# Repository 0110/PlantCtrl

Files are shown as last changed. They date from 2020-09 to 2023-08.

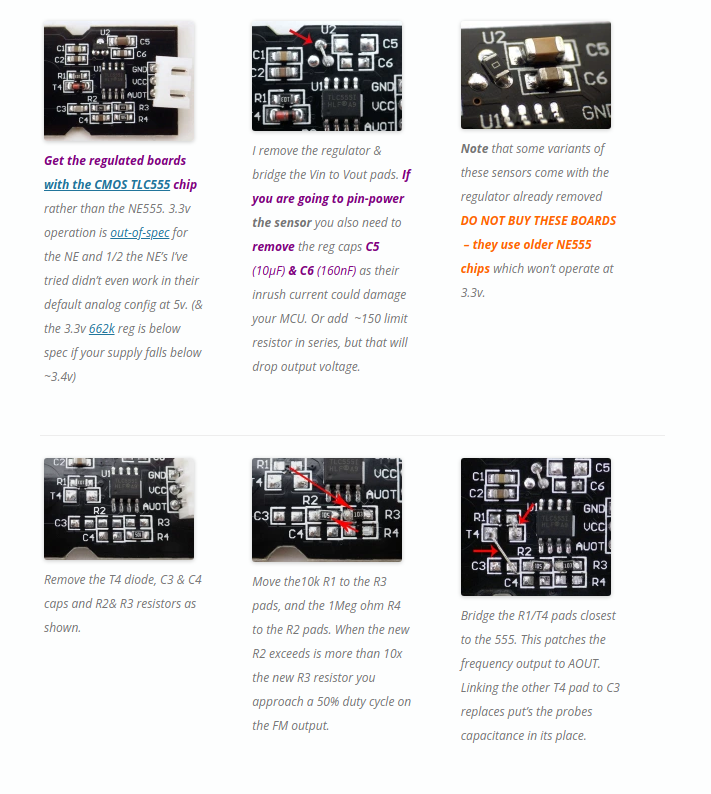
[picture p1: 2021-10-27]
hardware/sensor_mod.png

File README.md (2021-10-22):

# PlantCtrl

The following problems shall be solved with this project:
* Solar Powered
* Low Powered
* Plant monitoring
* Plant watering
* IoT

# Hardware
Open hardware design (powered by KiCAD).
The complete PCB is stored in the ***board*** sub directory.

There the following components are connected:
* ESP32 **16MB flash required**
* Lipo monitoring (DS2438)
* 7 moist sensors
* 7 pump
* DC-DC convert (generating voltage from Lipo for pumps)
* DS18B20 temperature sensors
* water level via laser distance sensor (VL53L0X)
* DS2438 battery monitor
* general purpose expansion pins

# Software
The firmware for the controller is stored in ***esp32*** sub directory.

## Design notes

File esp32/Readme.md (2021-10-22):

# PlantControl
## Hardware

Main processor
* ESP32 with 16MB Flash 

One-Wire
* Temperatur Sensor (DS18B20)
* Lipo-Monitoring (DS2438)

Lipo Protection
* Open drain 3.3V detector (CN61CN33 @ jlcpcb parts)

### Used Pins:
* See '''include/ControllerConfiguration.h'''

## Software
* MQTT topics

# Hardware
## Features
* Support for up to
 * 7 Moister sensors
 * 7 Pumps
 * Sensors
  * Solar powered (voltage)
  * Lipo-Powered (DS2438 for monitoring)
  * Temperature
  * Laser distance sensor [VL53L0X]
 * Custom GPIO

## Documentation of Power-Modes
https://lastminuteengineers.com/esp32-sleep-modes-power-consumption/#esp32-deep-sleep

gpio 17 only out no hold
gpio 16 only out no hold

## Additional hardware
solar charger 2A?
https://www.aliexpress.com/item/4000238259949.html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,searchweb201602_,searchweb201603_

MT3608 boost für pumpe
https://www.aliexpress.com/item/32925951391.html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,searchweb201602_,searchweb201603_

DS18B20 one wire temp sensor

# Features
## Empires Wunschliste
 * Pflanze
  * Pumpe
   * [x] Zeitspann (wann laufen darf)
   * [x] Helligkeitstrigger (Um den Morgen zum pumpen zu erkennen)
   * [-] Maximal Dauer zum Pumpen (als Zeit oder Milliliter)
   * [x] Zeitspanne zwischen zwei Pumpvorgängen
  * Moister sensor
   * [x] Schwellwert für Pumpe
* Tank
 * Füllstand Anzeige (in Liter)
 * Minimum Wasserstand (in cm damit Pumpen nicht leer laufen; enspricht 0 nutzbaren Liter)
 * [x] Maximaler Wasserstand des Tanks (in cm & Liter)

## Masterplan 2.0
 * Partitionslayout

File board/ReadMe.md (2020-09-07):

# ESP32 Plant Control Board

The board was built with manily through hole components for easy build and production with a mill.

## GPIO Mapping
See in the parent folder at **include/ControllerConfiguration.h**

## Routing
In order to use the the mill, the following parameter were used:
* Clearance 0.2mm
* Track width of 1.2mm or 1.0mm at minimum (when pins of a part are too close)

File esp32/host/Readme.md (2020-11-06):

# Configuration 
## File
Generate a file as, described in 
https://homieiot.github.io/homie-esp8266/docs/3.0.0/configuration/json-configuration-file/
For further details have a look at the Readme.md one level above.

## Upload
* Start ESP
* Login to Wifi, opened by the ESP
* Use the script to upload the configuration file
* restart the ESP

# Remote Upload

This script will allow you to send an OTA update to your device.

## Installation

Requirements are:
* paho-mqtt

## Usage

See ***upload-via-mqtt.sh***

# Remote Upload - Backend

## Usage

```text
usage: ota_updater.py [-h] -l BROKER_HOST -p BROKER_PORT [-u BROKER_USERNAME]
                      [-d BROKER_PASSWORD] [-t BASE_TOPIC] -i DEVICE_ID
                      firmware

ota firmware update scirpt for ESP8226 implemenation of the Homie mqtt IoT
convention.

positional arguments:
  firmware              path to the firmware to be sent to the device

arguments:
  -h, --help            show this help message and exit
  -l BROKER_HOST, --broker-host BROKER_HOST
                        host name or ip address of the mqtt broker
  -p BROKER_PORT, --broker-port BROKER_PORT
                        port of the mqtt broker
  -u BROKER_USERNAME, --broker-username BROKER_USERNAME
                        username used to authenticate with the mqtt broker
  -d BROKER_PASSWORD, --broker-password BROKER_PASSWORD
                        password used to authenticate with the mqtt broker
  -t BASE_TOPIC, --base-topic BASE_TOPIC
                        base topic of the homie devices on the broker
  -i DEVICE_ID, --device-id DEVICE_ID
                        homie device id
```

* `BROKER_HOST` and `BROKER_PORT` defaults to 127.0.0.1 and 1883 respectively if not set.
* `BROKER_USERNAME` and `BROKER_PASSWORD` are optional.
* `BASE_TOPIC` has to end with a slash, defaults to `homie/` if not set.

### Example:

```bash
python ota_updater.py -l localhost -u admin -d secure -t "homie/" -i "device-id" /path/to/firmware.bin
```

The Parameter can be extracted from the serial console
```serial
{} Stored configuration
  • Hardware device ID: 12345abcd
  • Device ID: MyDeviceId
  • Name: MyDeviceName
  • Device Stats Interval: 60 sec
  • Wi-Fi:
    ◦ SSID: MyWifi
    ◦ Password not shown
  • MQTT:
    ◦ Host: 192.168.0.2
    ◦ Port: 1883
    ◦ Base topic: /test/
    ◦ Auth? no
```

will result in the following command (when executed in this folder):
```bash
python ota_updater.py -l 192.168.0.2 -t "/test/" -i "MyDeviceId" ../.pio/build/esp32doit-devkit-v1/firmware.bin
```

### Source
https://github.com/homieiot/homie-esp8266/blob/develop/scripts/ota_updater

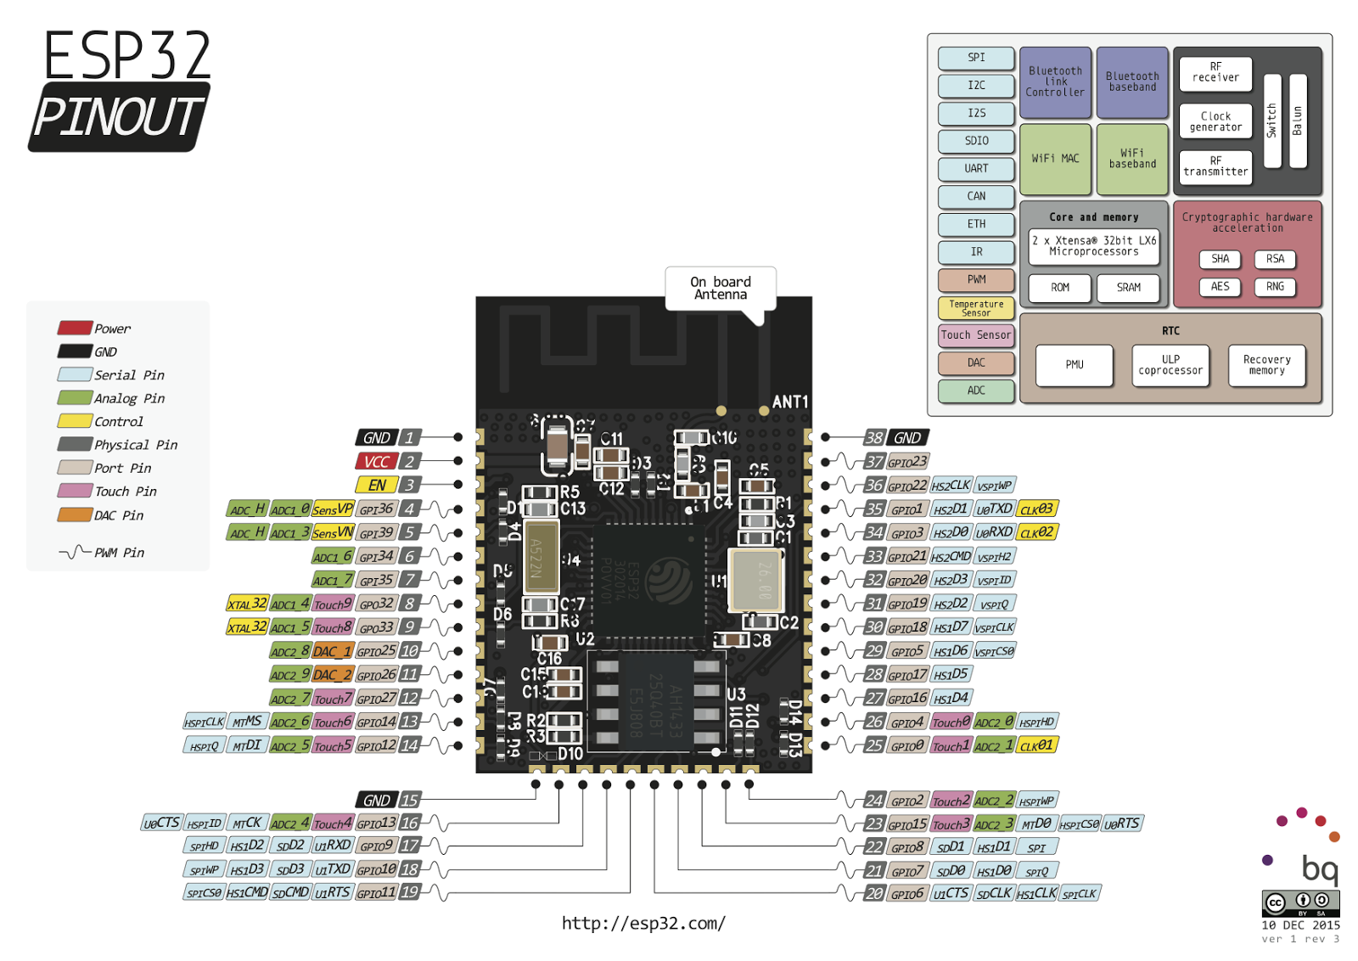
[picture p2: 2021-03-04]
sheets/esp32s.png

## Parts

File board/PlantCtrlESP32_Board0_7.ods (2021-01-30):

Reference | Value | Footprint | Datasheet | LCSC_PART_NUMBER | Field4 | Field5 | Field6 | DESCRIPTION | MANUFACTURER_PART_NUMBER
Shunt1 | 0.1 | Resistor_SMD:R_2512_6332Metric | ~ | C163067
R53 | 100 | Resistor_SMD:R_0805_2012Metric_Pad1.15x1.40mm_HandSolder | ~ | C17408
R11 | 270 | Resistor_SMD:R_0805_2012Metric_Pad1.15x1.40mm_HandSolder | ~ | C17590
R13 | 270 | Resistor_SMD:R_0805_2012Metric_Pad1.15x1.40mm_HandSolder | ~ | C17590
R15 | 270 | Resistor_SMD:R_0805_2012Metric_Pad1.15x1.40mm_HandSolder | ~ | C17590
R18 | 270 | Resistor_SMD:R_0805_2012Metric_Pad1.15x1.40mm_HandSolder | ~ | C17590
R30 | 270 | Resistor_SMD:R_0805_2012Metric_Pad1.15x1.40mm_HandSolder | ~ | C17590
R31 | 270 | Resistor_SMD:R_0805_2012Metric_Pad1.15x1.40mm_HandSolder | ~ | C17590
R5 | 270 | Resistor_SMD:R_0805_2012Metric_Pad1.15x1.40mm_HandSolder | ~ | C17590
R7 | 270 | Resistor_SMD:R_0805_2012Metric_Pad1.15x1.40mm_HandSolder | ~ | C17590
R9 | 270 | Resistor_SMD:R_0805_2012Metric_Pad1.15x1.40mm_HandSolder | ~ | C17590
R3 | 100k | Resistor_SMD:R_0805_2012Metric_Pad1.15x1.40mm_HandSolder | ~ | C702859
R54 | 100k | Resistor_SMD:R_0805_2012Metric_Pad1.15x1.40mm_HandSolder | ~ | C702859
C1 | 100n | Capacitor_SMD:C_0805_2012Metric_Pad1.15x1.40mm_HandSolder | ~ | C49678
C10 | 100n | Capacitor_SMD:C_0805_2012Metric_Pad1.15x1.40mm_HandSolder | ~ | C49678
C17 | 100n | Capacitor_SMD:C_0805_2012Metric_Pad1.15x1.40mm_HandSolder | ~ | C49678
C18 | 100n | Capacitor_SMD:C_0805_2012Metric_Pad1.15x1.40mm_HandSolder | ~ | C49678
C20 | 100n | Capacitor_SMD:C_0805_2012Metric_Pad1.15x1.40mm_HandSolder | ~ | C49678
C21 | 100n | Capacitor_SMD:C_0805_2012Metric_Pad1.15x1.40mm_HandSolder | ~ | C49678
C3 | 100n | Capacitor_SMD:C_0805_2012Metric_Pad1.15x1.40mm_HandSolder | ~ | C49678
C4 | 100n | Capacitor_SMD:C_0805_2012Metric_Pad1.15x1.40mm_HandSolder | ~ | C49678
C5 | 100n | Capacitor_SMD:C_0805_2012Metric_Pad1.15x1.40mm_HandSolder | ~ | C49678
C6 | 100n | Capacitor_SMD:C_0805_2012Metric_Pad1.15x1.40mm_HandSolder | ~ | C49678
C7 | 100n | Capacitor_SMD:C_0805_2012Metric_Pad1.15x1.40mm_HandSolder | ~ | C49678
C8 | 100n | Capacitor_SMD:C_0805_2012Metric_Pad1.15x1.40mm_HandSolder | ~ | C49678
C9 | 100n | Capacitor_SMD:C_0805_2012Metric_Pad1.15x1.40mm_HandSolder | ~ | C49678
R1 | 10k | Resistor_SMD:R_0805_2012Metric_Pad1.15x1.40mm_HandSolder | ~ | C212284
R12 | 10k | Resistor_SMD:R_0805_2012Metric_Pad1.15x1.40mm_HandSolder | ~ | C212284
R14 | 10k | Resistor_SMD:R_0805_2012Metric_Pad1.15x1.40mm_HandSolder | ~ | C212284
R16 | 10k | Resistor_SMD:R_0805_2012Metric_Pad1.15x1.40mm_HandSolder | ~ | C212284
R19 | 10k | Resistor_SMD:R_0805_2012Metric_Pad1.15x1.40mm_HandSolder | ~ | C212284
R2 | 10k | Resistor_SMD:R_0805_2012Metric_Pad1.15x1.40mm_HandSolder | ~ | C212284
R20 | 10k | Resistor_SMD:R_0805_2012Metric_Pad1.15x1.40mm_HandSolder | ~ | C212284
R22 | 10k | Resistor_SMD:R_0805_2012Metric_Pad1.15x1.40mm_HandSolder | ~ | C212284
R23 | 10k | Resistor_SMD:R_0805_2012Metric_Pad1.15x1.40mm_HandSolder | ~ | C212284
R24 | 10k | Resistor_SMD:R_0805_2012Metric_Pad1.15x1.40mm_HandSolder | ~ | C212284
R25 | 10k | Resistor_SMD:R_0805_2012Metric_Pad1.15x1.40mm_HandSolder | ~ | C212284
R27 | 10k | Resistor_SMD:R_0805_2012Metric_Pad1.15x1.40mm_HandSolder | ~ | C212284
R28 | 10k | Resistor_SMD:R_0805_2012Metric_Pad1.15x1.40mm_HandSolder | ~ | C212284
R32 | 10k | Resistor_SMD:R_0805_2012Metric_Pad1.15x1.40mm_HandSolder | ~ | C212284
R33 | 10k | Resistor_SMD:R_0805_2012Metric_Pad1.15x1.40mm_HandSolder | ~ | C212284
R35 | 1k | Resistor_SMD:R_0805_2012Metric_Pad1.15x1.40mm_HandSolder | ~ | C95781
R37 | 1k | Resistor_SMD:R_0805_2012Metric_Pad1.15x1.40mm_HandSolder | ~ | C95781
R4 | 10k | Resistor_SMD:R_0805_2012Metric_Pad1.15x1.40mm_HandSolder | ~ | C212284
R48 | 10k | Resistor_SMD:R_0805_2012Metric_Pad1.15x1.40mm_HandSolder | ~ | C212284
R58 | 10k | Resistor_SMD:R_0805_2012Metric_Pad1.15x1.40mm_HandSolder | ~ | C212284
R59 | 10k | Resistor_SMD:R_0805_2012Metric_Pad1.15x1.40mm_HandSolder | ~ | C212284
R6 | 10k | Resistor_SMD:R_0805_2012Metric_Pad1.15x1.40mm_HandSolder | ~ | C212284
R8 | 10k | Resistor_SMD:R_0805_2012Metric_Pad1.15x1.40mm_HandSolder | ~ | C212284
R21 | 19k-19.5K | Resistor_SMD:R_0805_2012Metric_Pad1.15x1.40mm_HandSolder | ~ | C17506
R29 | 1k | Resistor_SMD:R_0805_2012Metric_Pad1.15x1.40mm_HandSolder | ~ | C95781
R34 | 1k | Resistor_SMD:R_0805_2012Metric_Pad1.15x1.40mm_HandSolder | ~ | C95781
R36 | 1k | Resistor_SMD:R_0805_2012Metric_Pad1.15x1.40mm_HandSolder | ~ | C95781
R38 | 1k | Resistor_SMD:R_0805_2012Metric_Pad1.15x1.40mm_HandSolder | ~ | C95781
R39 | 1k | Resistor_SMD:R_0805_2012Metric_Pad1.15x1.40mm_HandSolder | ~ | C95781
R40 | 1k | Resistor_SMD:R_0805_2012Metric_Pad1.15x1.40mm_HandSolder | ~ | C95781
R41 | 1k | Resistor_SMD:R_0805_2012Metric_Pad1.15x1.40mm_HandSolder | ~ | C95781
R42 | 1k | Resistor_SMD:R_0805_2012Metric_Pad1.15x1.40mm_HandSolder | ~ | C95781
R43 | 1k | Resistor_SMD:R_0805_2012Metric_Pad1.15x1.40mm_HandSolder | ~ | C95781
R44 | 1k | Resistor_SMD:R_0805_2012Metric_Pad1.15x1.40mm_HandSolder | ~ | C95781
R45 | 1k | Resistor_SMD:R_0805_2012Metric_Pad1.15x1.40mm_HandSolder | ~ | C95781
R46 | 1k | Resistor_SMD:R_0805_2012Metric_Pad1.15x1.40mm_HandSolder | ~ | C95781
R47 | 1k | Resistor_SMD:R_0805_2012Metric_Pad1.15x1.40mm_HandSolder | ~ | C95781
R49 | 1k | Resistor_SMD:R_0805_2012Metric_Pad1.15x1.40mm_HandSolder | ~ | C95781
R50 | 1k | Resistor_SMD:R_0805_2012Metric_Pad1.15x1.40mm_HandSolder | ~ | C95781
R51 | 1k | Resistor_SMD:R_0805_2012Metric_Pad1.15x1.40mm_HandSolder | ~ | C95781
R52 | 1k | Resistor_SMD:R_0805_2012Metric_Pad1.15x1.40mm_HandSolder | ~ | C95781
C11 | 22uf | Capacitor_SMD:C_0805_2012Metric_Pad1.15x1.40mm_HandSolder | ~ | C45783
C12 | 22uf | Capacitor_SMD:C_0805_2012Metric_Pad1.15x1.40mm_HandSolder | ~ | C45783
C13 | 22uf | Capacitor_SMD:C_0805_2012Metric_Pad1.15x1.40mm_HandSolder | ~ | C45783
C14 | 22uf | Capacitor_SMD:C_0805_2012Metric_Pad1.15x1.40mm_HandSolder | ~ | C45783
C15 | 22uf | Capacitor_SMD:C_0805_2012Metric_Pad1.15x1.40mm_HandSolder | ~ | C45783
C16 | 22uf | Capacitor_SMD:C_0805_2012Metric_Pad1.15x1.40mm_HandSolder | ~ | C45783
C19 | 22uf | Capacitor_SMD:C_0805_2012Metric_Pad1.15x1.40mm_HandSolder | ~ | C45783
C2 | 22uf | Capacitor_SMD:C_0805_2012Metric_Pad1.15x1.40mm_HandSolder | ~ | C45783
D18 | 40V >2A | Diode_SMD:D_SOD-123F | ~ | C496544
D26 | 40V >2A | Diode_SMD:D_SOD-123F | ~ | C496544
D8 | 40V >2A | Diode_SMD:D_SOD-123F | ~ | C496544
R10 | 47k | Resistor_SMD:R_0805_2012Metric_Pad1.15x1.40mm_HandSolder | ~ | C17713
R17 | 47k | Resistor_SMD:R_0805_2012Metric_Pad1.15x1.40mm_HandSolder | ~ | C17713
L1 | 4A 5-22uH min DCR | Inductor_SMD:L_12x12mm_H4.5mm | ~ | C439398
R26 | 4k7 | Resistor_SMD:R_0805_2012Metric_Pad1.15x1.40mm_HandSolder | ~ | C17673
D10 | BAS40-04 | Package_TO_SOT_SMD:SOT-23 | http://www.vishay.com/docs/85701/bas40v.pdf | C397601
D11 | BAS40-04 | Package_TO_SOT_SMD:SOT-23 | http://www.vishay.com/docs/85701/bas40v.pdf | C397601
D12 | BAS40-04 | Package_TO_SOT_SMD:SOT-23 | http://www.vishay.com/docs/85701/bas40v.pdf | C397601
D13 | BAS40-04 | Package_TO_SOT_SMD:SOT-23 | http://www.vishay.com/docs/85701/bas40v.pdf | C397601
D14 | BAS40-04 | Package_TO_SOT_SMD:SOT-23 | http://www.vishay.com/docs/85701/bas40v.pdf | C397601
D15 | BAS40-04 | Package_TO_SOT_SMD:SOT-23 | http://www.vishay.com/docs/85701/bas40v.pdf | C397601
D16 | BAS40-04 | Package_TO_SOT_SMD:SOT-23 | http://www.vishay.com/docs/85701/bas40v.pdf | C397601
D17 | BAS40-04 | Package_TO_SOT_SMD:SOT-23 | http://www.vishay.com/docs/85701/bas40v.pdf | C397601
D19 | BAS40-04 | Package_TO_SOT_SMD:SOT-23 | http://www.vishay.com/docs/85701/bas40v.pdf | C397601
D20 | BAS40-04 | Package_TO_SOT_SMD:SOT-23 | http://www.vishay.com/docs/85701/bas40v.pdf | C397601
D21 | BAS40-04 | Package_TO_SOT_SMD:SOT-23 | http://www.vishay.com/docs/85701/bas40v.pdf | C397601
D22 | BAS40-04 | Package_TO_SOT_SMD:SOT-23 | http://www.vishay.com/docs/85701/bas40v.pdf | C397601
D23 | BAS40-04 | Package_TO_SOT_SMD:SOT-23 | http://www.vishay.com/docs/85701/bas40v.pdf | C397601
D24 | BAS40-04 | Package_TO_SOT_SMD:SOT-23 | http://www.vishay.com/docs/85701/bas40v.pdf | C397601
D25 | BAS40-04 | Package_TO_SOT_SMD:SOT-23 | http://www.vishay.com/docs/85701/bas40v.pdf | C397601
D9 | BAS40-04 | Package_TO_SOT_SMD:SOT-23 | http://www.vishay.com/docs/85701/bas40v.pdf | C397601
EXT_PWR1 | Conn_01x02 | Connector_JST:JST_XH_B2B-XH-A_1x02_P2.50mm_Vertical | ~
LIPO1 | Conn_01x02_Female | misc_footprints:BatteryHolder_Keystone_1042_1x18650 | ~
LIPO2 | Conn_01x02_Female | Connector_Wire:SolderWirePad_1x02_P5.08mm_Drill1.5mm | ~
PUMP0 | Conn_01x02_Female | Connector_JST:JST_EH_B2B-EH-A_1x02_P2.50mm_Vertical | ~
PUMP1 | Conn_01x02_Female | Connector_JST:JST_EH_B2B-EH-A_1x02_P2.50mm_Vertical | ~
PUMP2 | Conn_01x02_Female | Connector_JST:JST_EH_B2B-EH-A_1x02_P2.50mm_Vertical | ~
PUMP3 | Conn_01x02_Female | Connector_JST:JST_EH_B2B-EH-A_1x02_P2.50mm_Vertical | ~
PUMP4 | Conn_01x02_Female | Connector_JST:JST_EH_B2B-EH-A_1x02_P2.50mm_Vertical | ~
PUMP5 | Conn_01x02_Female | Connector_JST:JST_EH_B2B-EH-A_1x02_P2.50mm_Vertical | ~
PUMP6 | Conn_01x02_Female | Connector_JST:JST_EH_B2B-EH-A_1x02_P2.50mm_Vertical | ~
1WIRE1 | Conn_01x03 | Connector_JST:JST_EH_B3B-EH-A_1x03_P2.50mm_Vertical | ~
S0 | Conn_01x03_Male | Connector_JST:JST_EH_B3B-EH-A_1x03_P2.50mm_Vertical | ~
S1 | Conn_01x03_Male | Connector_JST:JST_EH_B3B-EH-A_1x03_P2.50mm_Vertical | ~
S2 | Conn_01x03_Male | Connector_JST:JST_EH_B3B-EH-A_1x03_P2.50mm_Vertical | ~
S3 | Conn_01x03_Male | Connector_JST:JST_EH_B3B-EH-A_1x03_P2.50mm_Vertical | ~
S4 | Conn_01x03_Male | Connector_JST:JST_EH_B3B-EH-A_1x03_P2.50mm_Vertical | ~
S5 | Conn_01x03_Male | Connector_JST:JST_EH_B3B-EH-A_1x03_P2.50mm_Vertical | ~
S6 | Conn_01x03_Male | Connector_JST:JST_EH_B3B-EH-A_1x03_P2.50mm_Vertical | ~
CUSTOM1 | Conn_01x04 | Connector_JST:JST_EH_B4B-EH-A_1x04_P2.50mm_Vertical | ~
DCDC1 | Conn_01x04 | Connector_PinSocket_2.54mm:PinSocket_1x04_P2.54mm_Vertical | ~
Hall1 | Conn_01x04 | ESP32:SR04M-2PinHeader_1x04_P2.54mm_Vertical | ~
SOLAR1 | Conn_01x04 | Connector_PinSocket_2.54mm:PinSocket_1x04_P2.54mm_Vertical | ~
I2C1 | Conn_01x04_Female | Connector_JST:JST_EH_B4B-EH-A_1x04_P2.50mm_Vertical | ~
GPIO1 | Conn_01x05_Female | Connector_JST:JST_EH_B5B-EH-A_1x05_P2.50mm_Vertical | ~
U1 | DS18B20 | Package_TO_SOT_THT:TO-92_Inline | http://datasheets.maximintegrated.com/en/ds/DS18B20.pdf
U2 | ds2438az+ | misc_footprints:ds2438az&plus_
IC1 | DW01 | misc_footprints:SOT95P280X135-6N |  | C14213 |  |  |  | ic | DW01
U5 | ESP32-WROOM-32D | RF_Module:ESP32-WROOM-32 | https://www.espressif.com/sites/default/files/documentation/esp32-wroom-32d_esp32-wroom-32u_datasheet_en.pdf | C529578
F1 | Fuse | Fuse:Fuseholder_Cylinder-5x20mm_Stelvio-Kontek_PTF78_Horizontal_Open | ~ | C58066
D2 | LED | LED_SMD:LED_0805_2012Metric_Pad1.15x1.40mm_HandSolder | ~ | C375452
D5 | LED | LED_SMD:LED_0805_2012Metric_Pad1.15x1.40mm_HandSolder | ~ | C375452
D6 | LED | LED_SMD:LED_0805_2012Metric_Pad1.15x1.40mm_HandSolder | ~ | C375452
D1 | LED_Blue | LED_SMD:LED_0805_2012Metric_Pad1.15x1.40mm_HandSolder | ~ | C205441
D3 | LED_Blue | LED_SMD:LED_0805_2012Metric_Pad1.15x1.40mm_HandSolder | ~ | C205441
D4 | LED_Blue | LED_SMD:LED_0805_2012Metric_Pad1.15x1.40mm_HandSolder | ~ | C205441
D7 | LED_Blue | LED_SMD:LED_0805_2012Metric_Pad1.15x1.40mm_HandSolder | ~ | C205441
Sensor1 | LED_green | LED_SMD:LED_0805_2012Metric_Pad1.15x1.40mm_HandSolder | ~ | C205442
Pumps1 | LED_red | LED_SMD:LED_0805_2012Metric_Pad1.15x1.40mm_HandSolder | ~ | C84256
U3 | LP38690DT-3.3 | ESP32:DPAK457P991X255-3N | IPC-7351B | C109045 | Texas Instruments | M | 2.55mm
Q1 | N-channel 30V 5A | Package_TO_SOT_SMD:SOT-23_Handsoldering |  | C350314 / C344010
Q10 | N-channel 30V 5A | Package_TO_SOT_SMD:SOT-23_Handsoldering |  | C350314 / C344010
Q11 | N-channel 30V 5A | Package_TO_SOT_SMD:SOT-23_Handsoldering |  | C350314 / C344010
Q12 | N-channel 30V 5A | Package_TO_SOT_SMD:SOT-23_Handsoldering |  | C350314 / C344010
Q2 | N-channel 30V 5A | Package_TO_SOT_SMD:SOT-23_Handsoldering |  | C350314 / C344010
Q3 | N-channel 30V 5A | Package_TO_SOT_SMD:SOT-23_Handsoldering |  | C350314 / C344010
Q4 | N-channel 30V 5A | Package_TO_SOT_SMD:SOT-23_Handsoldering |  | C350314 / C344010
Q5 | N-channel 30V 5A | Package_TO_SOT_SMD:SOT-23_Handsoldering |  | C350314 / C344010
Q6 | N-channel 30V 5A | Package_TO_SOT_SMD:SOT-23_Handsoldering |  | C350314 / C344010
Q7 | N-channel 30V 5A | Package_TO_SOT_SMD:SOT-23_Handsoldering |  | C350314 / C344010
Q8 | N-channel 30V 5A | Package_TO_SOT_SMD:SOT-23_Handsoldering |  | C350314 / C344010
Q9 | N-channel 30V 5A | Package_TO_SOT_SMD:SOT-23_Handsoldering |  | C350314
JP5 | NC | Jumper:SolderJumper-2_P1.3mm_Bridged_Pad1.0x1.5mm | ~
LED_SENS1 | NC | Jumper:SolderJumper-2_P1.3mm_Bridged_Pad1.0x1.5mm | ~
SOLAR_PWR1 | NC | Jumper:SolderJumper-2_P1.3mm_Bridged_Pad1.0x1.5mm | ~
Q_PWR1 | P-channel 50v 4A | Package_TO_SOT_SMD:SOT-23_Handsoldering |  | C344010
Q_PWR2 | P-channel 50v 4A | Package_TO_SOT_SMD:SOT-23_Handsoldering |  | C344010
Q_PWR3 | P-channel 50v 4A | Package_TO_SOT_SMD:SOT-23_Handsoldering |  | C344010
EXT_PWR2 | SolderJumper_2_Open | Jumper:SolderJumper-2_P1.3mm_Open_Pad1.0x1.5mm | ~
JP2 | SolderJumper_2_Open | Jumper:SolderJumper-2_P1.3mm_Open_Pad1.0x1.5mm | ~
OCP1 | SolderJumper_2_Open | Jumper:SolderJumper-2_P1.3mm_Open_Pad1.0x1.5mm | ~
SW1 | SW_Push | Button_Switch_SMD:SW_Push_1P1T_NO_CK_KMR2 | ~ | C72443
SW2 | SW_Push | Button_Switch_SMD:SW_Push_1P1T_NO_CK_KMR2 | ~ | C72443
U4 | SX1308 | misc_footprints:SOT-23-6 |  | C78162

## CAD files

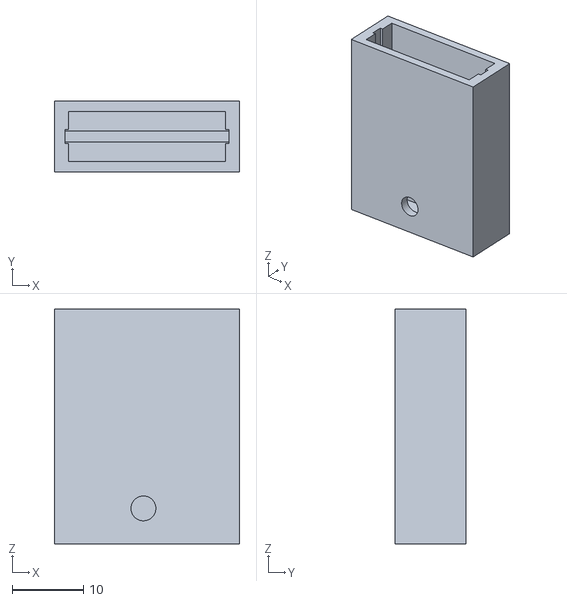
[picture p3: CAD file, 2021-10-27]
hardware/verguss form sensor v1.stl
26.0 x 10.0 x 33.0

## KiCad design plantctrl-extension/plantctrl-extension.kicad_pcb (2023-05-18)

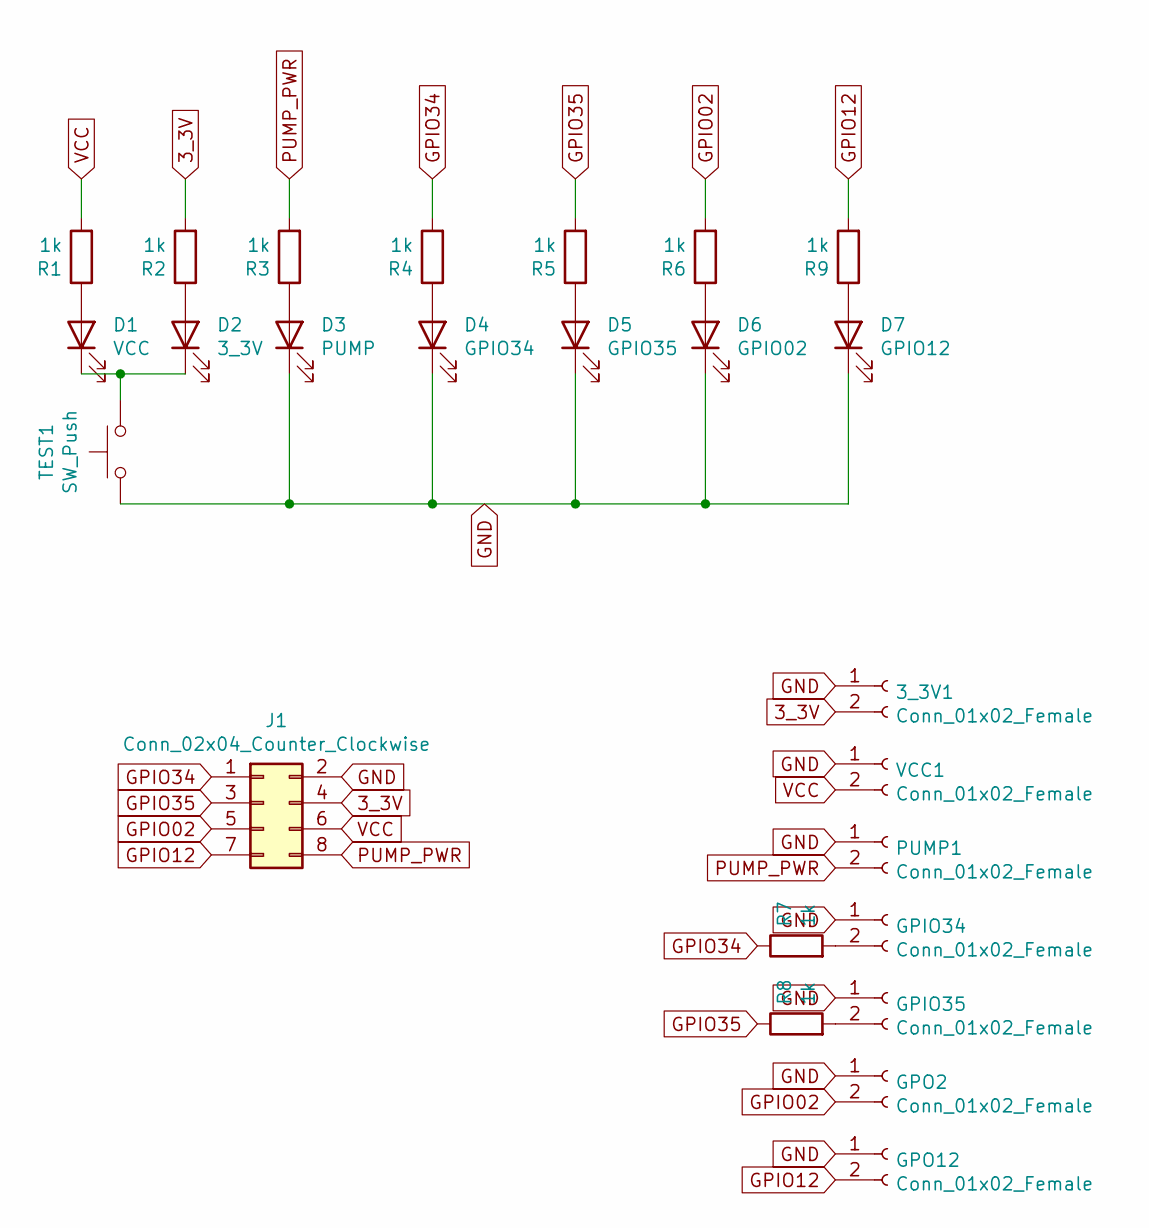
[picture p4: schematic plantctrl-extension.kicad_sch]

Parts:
3_3V1: Conn_01x02_Female; JST_EH_B2B-EH-A_1x02_P2.50mm_Vertical
D1: VCC; LED_0805_2012Metric; LCSC_PART_NUMBER C205441
D2: 3_3V; LED_0805_2012Metric; LCSC_PART_NUMBER C205441
D3: PUMP; LED_0805_2012Metric; LCSC_PART_NUMBER C205441
D4: GPIO34; LED_0805_2012Metric; LCSC_PART_NUMBER C205441
D5: GPIO35; LED_0805_2012Metric; LCSC_PART_NUMBER C205441
D6: GPIO02; LED_0805_2012Metric; LCSC_PART_NUMBER C205441
D7: GPIO12; LED_0805_2012Metric; LCSC_PART_NUMBER C205441
GPIO34, GPIO35: Conn_01x02_Female; JST_EH_B2B-EH-A_1x02_P2.50mm_Vertical
GPO2, GPO12: Conn_01x02_Female; JST_EH_B2B-EH-A_1x02_P2.50mm_Vertical
J1: Conn_02x04_Counter_Clockwise; PinSocket_2x04_P2.54mm_Vertical
PUMP1: Conn_01x02_Female; JST_EH_B2B-EH-A_1x02_P2.50mm_Vertical
R1, R2, R3, R4, R5, R6, R7, R8, R9: 1k; R_0805_2012Metric; LCSC_PART_NUMBER C95781
TEST1: SW_Push; SW_SPST_CK_RS282G05A3; LCSC_PART_NUMBER C72443
VCC1: Conn_01x02_Female; JST_EH_B2B-EH-A_1x02_P2.50mm_Vertical

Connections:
3_3V: 3_3V1.2, J1.4, R2.2
GND: 3_3V1.1, D3.1 (K), D4.1 (K), D5.1 (K), D6.1 (K), D7.1 (K), GPIO34.1, GPIO35.1, GPO2.1, GPO12.1, J1.2, PUMP1.1, TEST1.1, VCC1.1
GPIO02: GPO2.2, J1.5, R6.2
GPIO12: GPO12.2, J1.7, R9.2
GPIO34: J1.1, R4.2, R7.1
GPIO35: J1.3, R5.2, R8.1
unnamed: D1.2 (A), R1.1
unnamed: D2.2 (A), R2.1
unnamed: D3.2 (A), R3.1
unnamed: D4.2 (A), R4.1
unnamed: D5.2 (A), R5.1
unnamed: D6.2 (A), R6.1
unnamed: D7.2 (A), R9.1
unnamed: GPIO34.2, R7.2
unnamed: GPIO35.2, R8.2
unnamed: D1.1 (K), D2.1 (K), TEST1.2
PUMP_PWR: J1.8, PUMP1.2, R3.2
VCC: J1.6, R1.2, VCC1.2

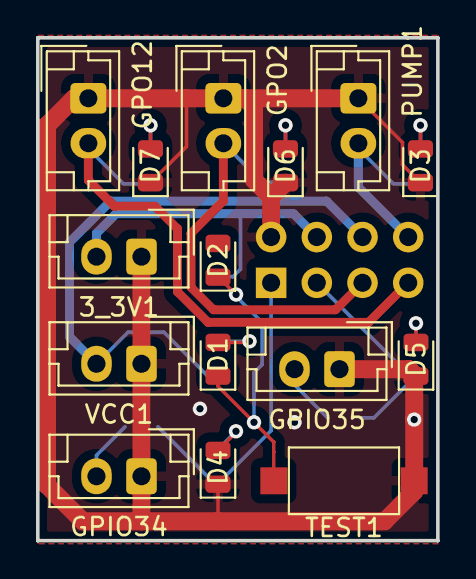
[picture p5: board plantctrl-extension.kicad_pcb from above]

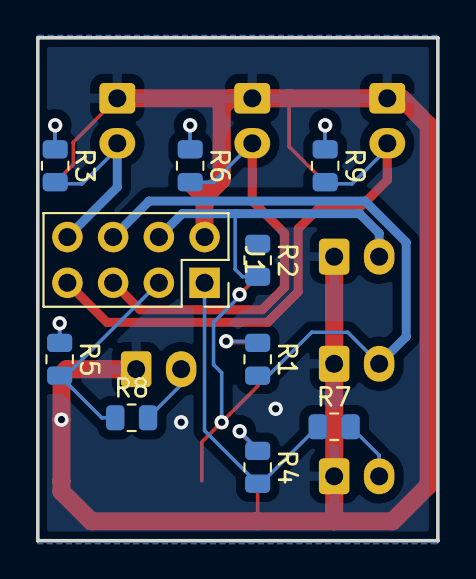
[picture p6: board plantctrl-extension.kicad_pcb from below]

Board: 2 copper layers, 22.2 x 27.9 mm, 25 parts (10 on the bottom side), 18 nets.

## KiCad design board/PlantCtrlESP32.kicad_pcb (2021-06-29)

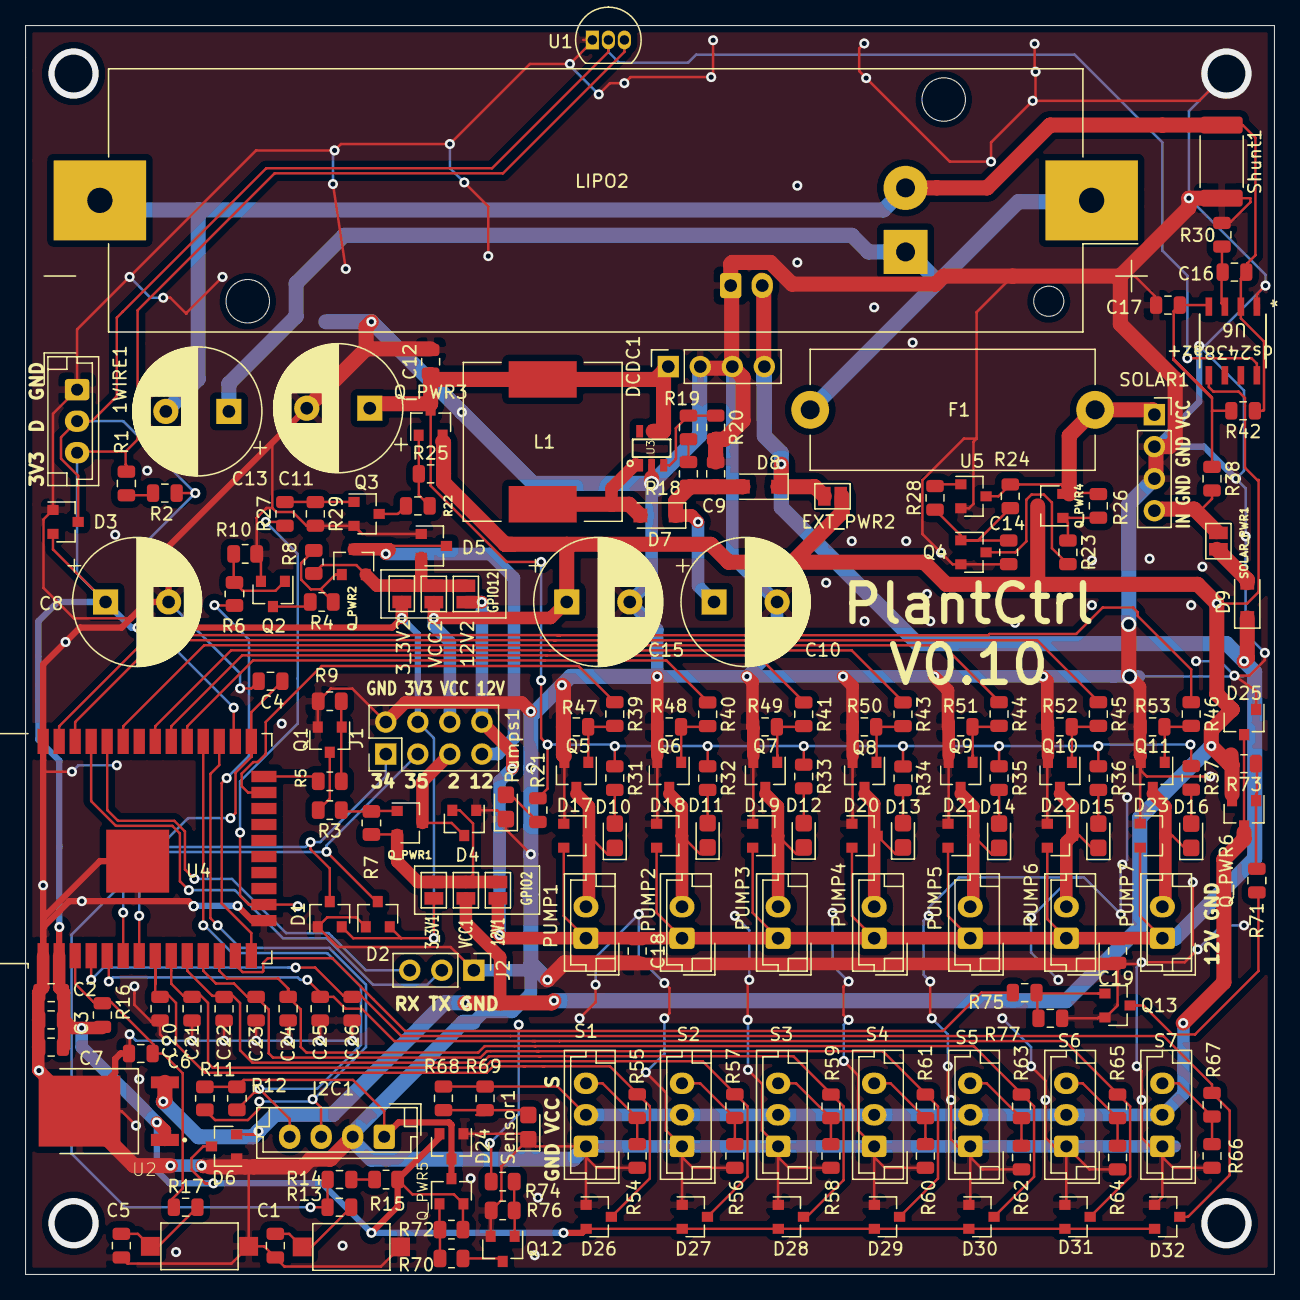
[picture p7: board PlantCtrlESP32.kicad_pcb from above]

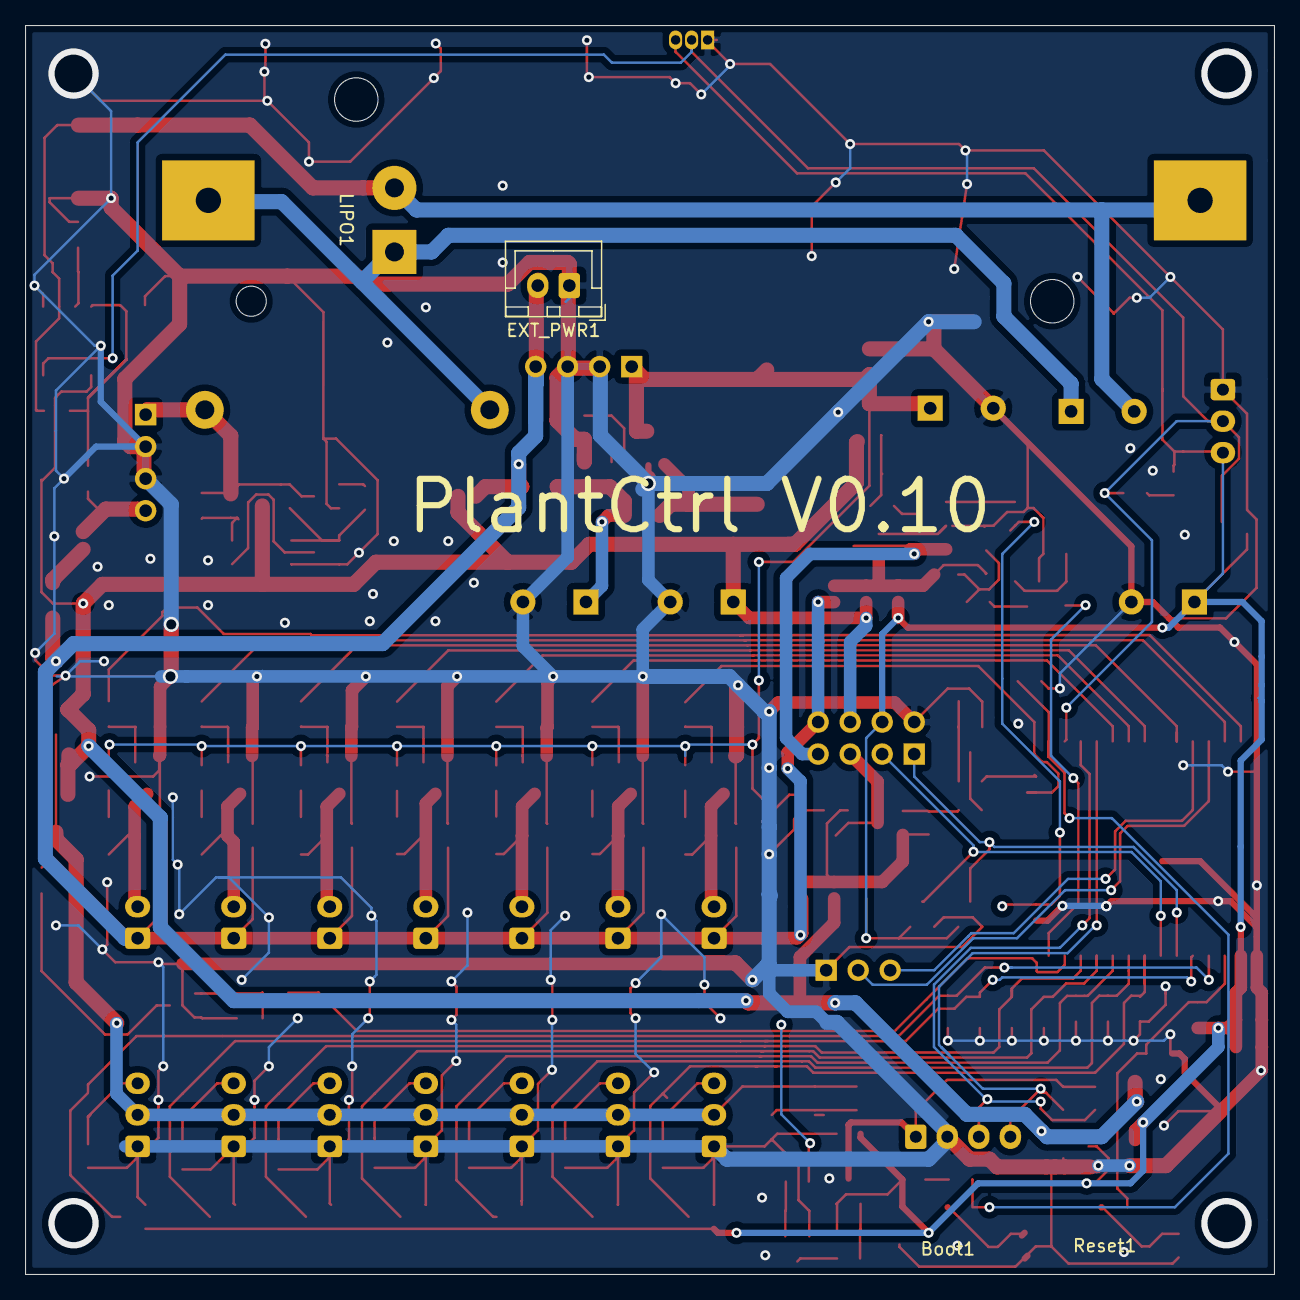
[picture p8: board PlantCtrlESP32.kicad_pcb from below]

Board: 2 copper layers, 99.1 x 99.1 mm, 198 parts (2 on the bottom side), 102 nets.

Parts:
1WIRE1: Conn_01x03; JST_EH_B3B-EH-A_1x03_P2.50mm_Vertical
3_3V1, 3_3V2, 12V1, 12V2: SolderJumper_2_Open; SolderJumper-2_P1.3mm_Open_Pad1.0x1.5mm
Boot1: Boot; SW_SPST_CK_RS282G05A3
C1, C2, C5, C14, C16, C17, C20, C21, C22, C23, C24, C25, C26: 100n; C_0805_2012Metric
C3, C4, C6, C7, C9, C12, C18, C19: 22uf; C_0805_2012Metric
C8, C10, C11, C13, C15: 1000uF; CP_Radial_D10.0mm_P5.00mm
D1, D2, D3, D4, D5, D6, D17, D18, D19, D20, D21, D22, D23, D24, D25, D26, D27, D28, D29, D30, D31, D32: BAS40-04; SOT-23
D7, D8, D9: 40V >2A; D_SOD-123F
D10, D12, D14, D16: LED_Blue; LED_0805_2012Metric_Castellated
D11, D13, D15: LED; LED_0805_2012Metric_Castellated
DCDC1: Conn_01x04; PinSocket_1x04_P2.54mm_Vertical
EXT_PWR1: Conn_01x02; JST_XH_B2B-XH-A_1x02_P2.50mm_Vertical
EXT_PWR2: SolderJumper_2_Open; SolderJumper-2_P1.3mm_Open_Pad1.0x1.5mm
F1: Fuse; Fuseholder_Cylinder-5x20mm_Stelvio-Kontek_PTF78_Horizontal_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
I2C1: Conn_01x04; JST_EH_B4B-EH-A_1x04_P2.50mm_Vertical
J1: Conn_02x04_Counter_Clockwise; PinHeader_2x04_P2.54mm_Vertical
J2: Conn_01x03_Female; PinHeader_1x03_P2.54mm_Vertical
L1: 4A 5-22uH min DCR; L_12x12mm_H4.5mm
LIPO1: Conn_01x02_Female; SolderWirePad_1x02_P5.08mm_Drill1.5mm
LIPO2: Conn_01x02_Female; BatteryHolder_Keystone_1042_1x18650
PUMP1, PUMP2, PUMP3, PUMP4, PUMP5, PUMP6, PUMP7: Conn_01x02_Female; JST_EH_B2B-EH-A_1x02_P2.50mm_Vertical
Pumps1: LED_red; LED_0805_2012Metric_Castellated
Q1, Q2, Q3, Q4, Q5, Q6, Q7, Q8, Q9, Q10, Q11, Q12, Q13: N-channel 30V 5A; SOT-23
Q_PWR1, Q_PWR2, Q_PWR3, Q_PWR4, Q_PWR5, Q_PWR6: P-channel 50v 4A; SOT-23
R1, R2, R3, R4, R5, R6, R13, R14, R15, R17, R20, R22, R23, R27, R28, R39, R40, R41, R42, R43, R44, R45, R46, R55, R57, R59, R61, R63, R65, R67, R70, R71, R74, R75: 1k; R_0805_2012Metric
R7, R8, R9, R10, R16, R18, R19, R25, R26, R29, R38, R47, R48, R49, R52, R53, R68, R69, R72, R73, R76, R77: 10k; R_0805_2012Metric
R11, R12: R; R_0805_2012Metric
R21, R31, R32, R33, R34, R35, R36, R37: 270; R_0805_2012Metric
R24, R30, R54, R56, R58, R60, R62, R64, R66: 100k; R_0805_2012Metric
R50, R51: 10K; R_0805_2012Metric
Reset1: SW_Push; SW_SPST_CK_RS282G05A3
S1, S2, S3, S4, S5, S6, S7: Conn_01x03_Male; JST_EH_B3B-EH-A_1x03_P2.50mm_Vertical
SOLAR1: Conn_01x04; PinSocket_1x04_P2.54mm_Vertical
SOLAR_PWR1: NO; SolderJumper-2_P1.3mm_Open_Pad1.0x1.5mm
Sensor1: LED_green; LED_0805_2012Metric_Castellated
Shunt1: 0.025; R_2512_6332Metric
U1: DS18B20; TO-92_Inline
U2: LP38690DT-3.3; DPAK457P991X255-3N
U3: SX1308; SOT-23-6
U4: ESP32-WROOM-32D; ESP32-WROOM-32
U5: CN61CN33; SOT-23
U6: ds2438az+; ds2438az&plus_
VCC1, VCC2: SolderJumper_2_Open; SolderJumper-2_P1.3mm_Open_Pad1.0x1.5mm

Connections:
3_3V: 1WIRE1.3, 3_3V1.2, 3_3V2.2, C2.2, C3.1, C7.1, C8.1, D1.2, D2.2, D3.2, D6.3, D24.2, D26.2, D27.2, D28.2, D29.2, D30.2, D31.2, D32.2, J1.4, Q_PWR5.2, R1.2, R15.2, R16.2, R72.2, U1.3, U2.1, U4.2
CUSTOM_GPIO2: R5.2, U4.24
CUSTOM_GPIO12: R6.2, U4.14
CUSTOM_GPIO34: D1.3, J1.1, U4.6
CUSTOM_GPIO35: D2.3, J1.3, U4.7
ESP_RX: J2.3, U4.34
ESP_TX: J2.2, U4.35
GND: 1WIRE1.1, Boot1.1, C1.1, C2.1, C3.2, C4.1, C5.1, C6.1, C7.2, C8.2, C9.2, C10.2, C11.2, C12.2, C14.1, C15.2, C17.2, C18.2, C19.2, C20.1, C21.1, C22.1, C23.1, C24.1, C25.1, C26.1, D1.1, D2.1, D3.1, D4.1, D5.1, D6.1, D17.1, D18.1, D19.1, D20.1, D21.1, D22.1, D23.1, D24.1, D25.1, D26.1, D27.1, D28.1, D29.1, D30.1, D31.1, D32.1, DCDC1.2, DCDC1.3, EXT_PWR1.1, I2C1.2, J1.2, J2.1, Pumps1.1, Q1.2, Q2.2, Q3.2, Q4.2, Q5.2, Q6.2, Q7.2, Q8.2, Q9.2, Q10.2, Q11.2, Q12.2, Q13.2, R9.2, R10.2, R20.2, R29.2, R30.1, R47.2, R48.1, R49.2, R50.2, R51.2, R52.2, R53.2, R54.1, R56.1, R58.1, R60.1, R62.1, R64.1, R66.1, R76.2, R77.2, Reset1.1, S1.1, S2.1, S3.1, S4.1, S5.1, S6.1, S7.1, SOLAR1.2, SOLAR1.3, Sensor1.1, Shunt1.2, U1.1, U2.4, U3.2, U4.1, U4.15, U4.38, U4.39, U5.2, U6.1
unnamed: 3_3V1.1, 12V1.1, D4.2, Q_PWR1.2, R7.2, VCC1.1
unnamed: 3_3V2.1, 12V2.1, D5.2, Q_PWR2.2, R8.2, VCC2.1
unnamed: Boot1.2, C1.2, R13.2
unnamed: C4.2, R13.1, R14.1, U4.25
unnamed: C5.2, R17.2, Reset1.2
unnamed: C6.2, R16.1, R17.1, U4.3
unnamed: C9.1, C10.1, D7.1, D8.2, R18.1
unnamed: C14.2, Q4.1, R24.2, R28.1
unnamed: C16.1, R30.2, U6.3
unnamed: C17.1, R38.1, R42.2, U6.4
unnamed: D4.3, J1.5, Q_PWR1.3
unnamed: D5.3, J1.7, Q_PWR2.3
unnamed: D7.2, L1.2, U3.1
unnamed: D9.2, SOLAR_PWR1.1
unnamed: D10.2, R31.2
unnamed: D11.2, R32.2
unnamed: D12.2, R33.2
unnamed: D13.2, R34.2
unnamed: D14.2, R35.2
unnamed: D15.2, R36.2
unnamed: D16.2, R37.2
unnamed: Pumps1.2, R21.2
unnamed: Q1.1, R5.1, R9.1
unnamed: Q1.3, R3.2
unnamed: Q2.1, R6.1, R10.1
unnamed: Q2.3, R4.2
unnamed: Q3.1, R27.1, R29.1
unnamed: Q3.3, R22.2
unnamed: Q4.3, R23.2
unnamed: Q5.1, R39.2, R47.1
unnamed: Q6.1, R40.2, R48.2
unnamed: Q7.1, R41.2, R49.1
unnamed: Q8.1, R43.2, R50.1
unnamed: Q9.1, R44.2, R51.1
unnamed: Q10.1, R45.2, R52.1
unnamed: Q11.1, R46.2, R53.1
unnamed: Q12.1, R74.1, R76.1
unnamed: Q12.3, R70.2
unnamed: Q13.1, R75.1, R77.1
unnamed: Q13.3, R71.2
unnamed: Q_PWR1.1, R3.1, R7.1
unnamed: Q_PWR2.1, R4.1, R8.1
unnamed: Q_PWR3.1, R22.1, R25.1
unnamed: Q_PWR4.1, R23.1, R26.1
unnamed: Q_PWR5.1, R70.1, R72.1
unnamed: Q_PWR6.1, R71.1, R73.1
unnamed: R1.1, R2.1
unnamed: R14.2, R15.1
unnamed: R18.2, R19.1
unnamed: R19.2, R20.1, U3.3
unnamed: R28.2, U5.1
unnamed: R54.2, R55.1, S1.3
unnamed: R56.2, R57.1, S2.3
unnamed: R58.2, R59.1, S3.3
unnamed: R60.2, R61.1, S4.3
unnamed: R62.2, R63.1, S5.3
unnamed: R64.2, R65.1, S6.3
unnamed: R66.2, R67.1, S7.3
unnamed: R68.1, R69.1, Sensor1.2
PLANT0_MOIST: C20.2, D26.3, R55.2, U4.8
PLANT0_PUMP: D10.1, D17.3, PUMP1.2, Q5.3
PLANT1_MOIST: C21.2, D27.3, R57.2, U4.9
PLANT1_PUMP: D11.1, D18.3, PUMP2.2, Q6.3
PLANT2_MOIST: C22.2, D28.3, R59.2, U4.10
PLANT2_PUMP: D12.1, D19.3, PUMP3.2, Q7.3
PLANT3_MOIST: C23.2, D29.3, R61.2, U4.11
PLANT3_PUMP: D13.1, D20.3, PUMP4.2, Q8.3
PLANT4_MOIST: C24.2, D30.3, R63.2, U4.12
PLANT4_PUMP: D14.1, D21.3, PUMP5.2, Q9.3
PLANT5_MOIST: C25.2, D31.3, R65.2, U4.5
PLANT5_PUMP: D15.1, D22.3, PUMP6.2, Q10.3
PLANT6_MOIST: C26.2, D32.3, R67.2, U4.4
PLANT6_PUMP: D16.1, D23.3, PUMP7.2, Q11.3
PLANT_CTRL_PUMP_0: R39.1, U4.23
PLANT_CTRL_PUMP_1: R40.1, U4.29
PLANT_CTRL_PUMP_2: R41.1, U4.30
PLANT_CTRL_PUMP_3: R43.1, U4.31
PLANT_CTRL_PUMP_4: R44.1, U4.33
PLANT_CTRL_PUMP_5: R45.1, U4.36
PLANT_CTRL_PUMP_6: R46.1, U4.37
PUMP_ENABLE: R27.2, U4.16
PUMP_PWR: 12V1.2, 12V2.2, C18.1, C19.1, D8.1, D9.1, D17.2, D18.2, D19.2, D20.2, D21.2, D22.2, D23.2, DCDC1.4, EXT_PWR1.2, EXT_PWR2.1, J1.8, PUMP1.1, PUMP2.1, PUMP3.1, PUMP4.1, PUMP5.1, PUMP6.1, PUMP7.1
PWR_I2C: D24.3, I2C1.1, Q_PWR5.3, R11.1, R12.1
PWR_PUMP_CONVERTER: C11.1, C12.1, DCDC1.1, L1.1, Q_PWR3.3, R21.1, R31.1, R32.1, R33.1, R34.1, R35.1, R36.1, R37.1, U3.4, U3.5
PWR_SENSORS: D25.3, Q_PWR6.3, R68.2, R69.2, S1.2, S2.2, S3.2, S4.2, S5.2, S6.2, S7.2
Rsense+: C13.2, C16.2, LIPO1.2, LIPO2.2, R42.1, Shunt1.1, U6.2
SCL: I2C1.3, R11.2, U4.27
SDA: I2C1.4, R12.2, U4.28
SENSORS_ENABLE: R74.2, R75.2, U4.13
SOLAR_IN: R38.2, SOLAR1.4, SOLAR_PWR1.2
Temp: 1WIRE1.2, D3.3, R2.2, U1.2, U4.26, U6.8
VCC: C15.1, D6.2, D25.2, EXT_PWR2.2, J1.6, Q_PWR3.2, Q_PWR4.3, Q_PWR6.2, R25.2, R73.2, U2.3, U6.5, VCC1.2, VCC2.2
VCC_BATT: C13.1, F1.2, LIPO1.1, LIPO2.1
VCC_FUSED_ALWAYS: F1.1, Q_PWR4.2, R24.1, R26.2, SOLAR1.1, U5.3

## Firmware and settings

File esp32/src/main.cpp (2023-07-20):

/** \addtogroup Controller
 *  @{
 *
 * @file main.cpp
 * @author Ollo
 * @brief PlantControl
 * @version 0.1
 * @date 2020-05-01
 *
 * @copyright Copyright (c) 2020
 */

/******************************************************************************
 *                                     INCLUDES
 ******************************************************************************/
#define CONFIG_APP_ROLLBACK_ENABLE
#include "LogDefines.h"
#include "FileUtils.h"
#include "TimeUtils.h"
#include "PlantCtrl.h"
#include "ControllerConfiguration.h"
#include "HomieConfiguration.h"
#include "DallasTemperature.h"
#include <Homie.h>
#include "time.h"
#include "esp_sleep.h"
#include "RunningMedian.h"
#include "WakeReason.h"
#include <stdint.h>
#include <math.h>
#include <OneWire.h>
#include "DS2438.h"
#include "soc/soc.h"
#include "soc/rtc_cntl_reg.h"
#include <Wire.h>
#include <VL53L0X.h>
#include "driver/pcnt.h"
#include "MQTTUtils.h"
#include "esp_ota_ops.h"
#include "Arduino.h"

extern "C" bool verifyRollbackLater(){
    return true;
}

#if defined(TIMED_LIGHT_PIN)
#include "ulp-pwm.h"
#endif

/******************************************************************************
 *                                     DEFINES
 ******************************************************************************/
#define AMOUNT_SENOR_QUERYS 8
#define MAX_TANK_DEPTH 5000
#define REBOOT_LOOP_DETECTION_ERROR 5

/******************************************************************************
 *                            FUNCTION PROTOTYPES
 ******************************************************************************/

int determineNextPump(bool lowLight);
void plantcontrol();
void readPowerSwitchedSensors();
bool determineTimedLightState(bool lowLight);
bool otaRunning = false;

/******************************************************************************
 *                       NON VOLATILE VARIABLES in DEEP SLEEP
 ******************************************************************************/
#if defined(TIMED_LIGHT_PIN)
RTC_DATA_ATTR bool timedLightLowVoltageTriggered = false; /**remember if it was shut down due to voltage level */
#endif                                                    // TIMED_LIGHT_PIN

RTC_DATA_ATTR long rtcLastWateringPlant[MAX_PLANTS] = {0};
RTC_DATA_ATTR long consecutiveWateringPlant[MAX_PLANTS] = {0};

/******************************************************************************
 *                            LOCAL VARIABLES
 ******************************************************************************/
bool volatile mDownloadMode = false; /**< Controller must not sleep */
bool volatile mSensorsRead = false;  /**< Sensors are read without Wifi or MQTT */
int volatile pumpToRun = -1;         /** pump to run  at the end of the cycle */
int volatile selfTestPumpRun = -1;   /** pump to run  at the end of the cycle */

bool mConfigured = false;
long nextBlink = 0; /**< Time needed in main loop to support expected blink code */

RunningMedian waterRawSensor = RunningMedian(WATERSENSOR_CYCLE);
float mSolarVoltage = 0.0f; /**< Voltage from solar panels */
float mBatteryVoltage = 0.0f; /**< Voltage from lipo */
unsigned long setupFinishedTimestamp;

bool pumpStarted = false;
long pumpTarget = -1;
long pumpStartTime = 0;
long lastSendPumpUpdate = 0;
#ifdef FLOWMETER_PIN
long pumpTargetMl = -1;
#endif

float waterTemp = 30;

/*************************** Hardware abstraction *****************************/

OneWire oneWire(SENSOR_ONEWIRE);
DallasTemperature sensors(&oneWire);
DS2438 battery(&oneWire, 0.0333333f, AMOUNT_SENOR_QUERYS);
VL53L0X tankSensor;

#ifndef PLANT0_SENSORTYPE
#error "Sensor type must be specified, see HomieTypes.h - Sensor types"
#endif
#ifndef PLANT1_SENSORTYPE
#error "Sensor type must be specified, see HomieTypes.h - Sensor types"
#endif
#ifndef PLANT2_SENSORTYPE
#error "Sensor type must be specified, see HomieTypes.h - Sensor types"
#endif
#ifndef PLANT3_SENSORTYPE
#error "Sensor type must be specified, see HomieTypes.h - Sensor types"
#endif
#ifndef PLANT4_SENSORTYPE
#error "Sensor type must be specified, see HomieTypes.h - Sensor types"
#endif
#ifndef PLANT5_SENSORTYPE
#error "Sensor type must be specified, see HomieTypes.h - Sensor types"
#endif
#ifndef PLANT6_SENSORTYPE
#error "Sensor type must be specified, see HomieTypes.h - Sensor types"
#endif

Plant mPlants[MAX_PLANTS] = {
    Plant(SENSOR_PLANT0, OUTPUT_PUMP0, 0, &plant0, &mSetting0, PLANT0_SENSORTYPE),
    Plant(SENSOR_PLANT1, OUTPUT_PUMP1, 1, &plant1, &mSetting1, PLANT1_SENSORTYPE),
    Plant(SENSOR_PLANT2, OUTPUT_PUMP2, 2, &plant2, &mSetting2, PLANT2_SENSORTYPE),
    Plant(SENSOR_PLANT3, OUTPUT_PUMP3, 3, &plant3, &mSetting3, PLANT3_SENSORTYPE),
    Plant(SENSOR_PLANT4, OUTPUT_PUMP4, 4, &plant4, &mSetting4, PLANT4_SENSORTYPE),
    Plant(SENSOR_PLANT5, OUTPUT_PUMP5, 5, &plant5, &mSetting5, PLANT5_SENSORTYPE),
    Plant(SENSOR_PLANT6, OUTPUT_PUMP6, 6, &plant6, &mSetting6, PLANT6_SENSORTYPE)};

/******************************************************************************
 *                            LOCAL FUNCTIONS
 ******************************************************************************/

void finsihedCycleSucessfully()
{
  const esp_partition_t *running = esp_ota_get_running_partition();
  esp_ota_img_states_t ota_state;
  if (esp_ota_get_state_partition(running, &ota_state) == ESP_OK)
  {
    log(LOG_LEVEL_INFO, "Get State Partition was Successfull", LOG_BOOT_ERROR_DETECTION); 
    
    if(ota_state == ESP_OTA_IMG_UNDEFINED){
      log(LOG_LEVEL_INFO, "ESP_OTA_IMG_UNDEFINED should not happen with rollback", LOG_BOOT_ERROR_DETECTION);
    }
    if(ota_state == ESP_OTA_IMG_NEW){
      log(LOG_LEVEL_INFO, "ESP_OTA_IMG_NEW", LOG_BOOT_ERROR_DETECTION);
    }
    if(ota_state == ESP_OTA_IMG_INVALID){
      log(LOG_LEVEL_INFO, "ESP_OTA_IMG_INVALID", LOG_BOOT_ERROR_DETECTION);
    }
    if(ota_state == ESP_OTA_IMG_VALID){
      log(LOG_LEVEL_INFO, "ESP_OTA_IMG_VALID", LOG_BOOT_ERROR_DETECTION);
    }
    if (ota_state == ESP_OTA_IMG_PENDING_VERIFY)
    {
      log(LOG_LEVEL_INFO, "ESP_OTA_IMG_PENDING_VERIFY Diagnostics completed successfully! Marking as valid", LOG_BOOT_ERROR_DETECTION);
      esp_ota_mark_app_valid_cancel_rollback();
    }
  }
}

void espDeepSleep(bool afterPump = false)
{
  if (mDownloadMode)
  {
    log(LOG_LEVEL_DEBUG, "abort deepsleep, DownloadMode active", LOG_DEBUG_CODE);
    // if we manage to get to the download mode, the device can be restored
    finsihedCycleSucessfully();
    return;
  }
  if (aliveWasRead())
  {
    for (int i = 0; i < 10; i++)
    {
      long cTime = getCurrentTime();
      if (cTime < 100000)
      {
        delay(100);
      }
      else
      {
        break;
      }
    }
    if (getCurrentTime() < 100000)
    {
      log(LOG_LEVEL_DEBUG, "NTP timeout before deepsleep", LOG_DEBUG_CODE);
    }
  }

  esp_sleep_pd_config(ESP_PD_DOMAIN_RTC_PERIPH, ESP_PD_OPTION_ON);

  long secondsToSleep = -1;

  if (afterPump)
  {
    log(LOG_LEVEL_INFO, "AfterPump Cycle Resume", LOG_SLEEP_CYCLE);
    secondsToSleep = 1;
  }
  else
  {
    if (mBatteryVoltage < VOLT_MIN_BATT) 
    {
      log(LOG_LEVEL_INFO, String(String(mBatteryVoltage) + "V! Almost empty -> deepSleepNight " + String(LOWVOLT_SLEEP_FACTOR)) + " times", LOG_SLEEP_LOWVOLTAGE);
      /* use the largest sleeping duration */
      if (deepSleepNightTime.get() > deepSleepTime.get()) {
        secondsToSleep = (deepSleepNightTime.get() * LOWVOLT_SLEEP_FACTOR);
      } else {
        secondsToSleep = (deepSleepTime.get() * LOWVOLT_SLEEP_FACTOR);
      }
      /* sleep at least several minutes, so the solar panel can charge the battery */
      if (secondsToSleep < LOWVOLT_SLEEP_MINIMUM) {
        secondsToSleep = LOWVOLT_SLEEP_MINIMUM;
      }
    }
    else if (mSolarVoltage < SOLAR_CHARGE_MIN_VOLTAGE)
    {
      log(LOG_LEVEL_INFO, String(String(mSolarVoltage) + "V! Low light -> deepSleepNight"), LOG_SLEEP_NIGHT);
      secondsToSleep = deepSleepNightTime.get();
    }
    else
    {
      log(LOG_LEVEL_INFO, "Sunny -> deepSleep", LOG_SLEEP_DAY);
      secondsToSleep = deepSleepTime.get();
    }
  }

  finsihedCycleSucessfully();
  /* sleep always at least one second */
  if (secondsToSleep < 0) {
    secondsToSleep = 1;
  }
  esp_sleep_enable_timer_wakeup((secondsToSleep * 1000U * 1000U));
  if (aliveWasRead())
  {
    delay(1000);
    Homie.prepareToSleep();
  }
  else
  {
    esp_deep_sleep_start();
  }
}

// requires homie being started
void readOneWireSensors()
{
  for (uint8_t i = 0; i < sensors.getDeviceCount(); i++)
  {
    uint8_t ds18b20Address[8];
    bool valid = false;
    float temp = -127;
    for (int retry = 0; retry < AMOUNT_SENOR_QUERYS && !valid; retry++)
    {
      bool validAddress = sensors.getAddress(ds18b20Address, i);
      if (validAddress && sensors.validFamily(ds18b20Address))
      {
        temp = sensors.getTempC(ds18b20Address);
        if (temp != -127)
        {
          valid = true;
        }
        else
        {
          delay(10);
        }
      }
    }

    if (!valid)
    {
      // wrong family or crc errors on each retry
      continue;
   }
   char buf[(sizeof(ds18b20Address) * 2) + 1]; /* additional byte for trailing terminator */
    snprintf(buf, sizeof(buf), "%.2X%.2X%.2X%.2X%.2X%.2X%.2X%.2X",
             ds18b20Address[0],
             ds18b20Address[1],
             ds18b20Address[2],
             ds18b20Address[3],
             ds18b20Address[4],
             ds18b20Address[5],
             ds18b20Address[6],
             ds18b20Address[7]);
   if (valid)
    {
      Serial << "DS18S20 Temperatur " << String(buf) << " : " << temp << " °C " << endl;
      if (strcmp(lipoSensorAddr.get(), buf) == 0)
      {
        mqttWrite(&sensorTemp, TEMPERATUR_SENSOR_LIPO, String(temp));
        Serial << "Lipo Temperatur " << temp << " °C " << endl;
      }
      if (strcmp(waterSensorAddr.get(), buf) == 0)
      {
        mqttWrite(&sensorTemp, TEMPERATUR_SENSOR_WATER, String(temp));
        Serial << "Water Temperatur " << temp << " °C " << endl;
        waterTemp = temp;
      }
      /* Always send the sensor address with the temperatur value */
      mqttWrite(&sensorTemp, String(buf), String(temp));
    }
    else
    {
      Serial << "DS18S20 sensor " << String(buf) << " could not be read " << temp << endl;
    }
  }

  battery.updateMultiple();
  mSolarVoltage = battery.getVoltage(BATTSENSOR_INDEX_SOLAR) * SOLAR_VOLT_FACTOR;

  Serial.flush();
}

/**
 * @brief Sensors, that are connected to GPIOs, mandatory for WIFI.
 * These sensors (ADC2) can only be read when no Wifi is used.
 */
void readPowerSwitchedSensors()
{
  for (int i = 0; i < MAX_PLANTS; i++)
  {
    Serial << "Sensor " << i << " mode:  " << mPlants[i].getSensorModeString() << endl;
  }
  digitalWrite(OUTPUT_ENABLE_SENSOR, HIGH);
  delay(50);
  for (int i = 0; i < MAX_PLANTS; i++)
  {
    mPlants[i].startMoistureMeasurement();
  }
  delay(MOISTURE_MEASUREMENT_DURATION);
  for (int i = 0; i < MAX_PLANTS; i++)
  {
    mPlants[i].stopMoistureMeasurement();
  }

  for (int i = 0; i < MAX_PLANTS; i++)
  {
    mPlants[i].blockingMoistureMeasurement();
  }

  for (int i = 0; i < MAX_PLANTS; i++)
  {
    Plant plant = mPlants[i];
    switch (plant.getSensorMode())
    {
      case FREQUENCY_MOD_RESISTANCE_PROBE: {
        Serial << "Plant " << i << " measurement: " << mPlants[i].getCurrentMoistureRaw() << " hz " << mPlants[i].getCurrentMoisturePCT() << "%" <<  endl;
        break;
      }
      case ANALOG_RESISTANCE_PROBE : {
        Serial << "Plant " << i << " measurement: " << mPlants[i].getCurrentMoistureRaw() << " mV " << mPlants[i].getCurrentMoisturePCT() << "%" <<  endl;
        break;
      }
      case NONE : {

      }
    }
  }

  Wire.begin(SENSOR_TANK_SDA, SENSOR_TANK_SCL);
  // Source: https://www.st.com/resource/en/datasheet/vl53l0x.pdf
  tankSensor.setAddress(0x52);
  tankSensor.setBus(&Wire);
  delay(50);
  Serial << "Distance sensor init" << endl;
  long start = millis();
  bool distanceReady = false;
  while ((start + WATERSENSOR_TIMEOUT) > millis())
  {
    if (tankSensor.init())
    {
      distanceReady = true;
      break;
    }
    else
    {
      delay(200);
    }
  }
  if (distanceReady)
  {
    waterRawSensor.clear();
    tankSensor.setSignalRateLimit(0.1);
    // increase laser pulse periods (defaults are 14 and 10 PCLKs)
    tankSensor.setVcselPulsePeriod(VL53L0X::VcselPeriodPreRange, 18);
    tankSensor.setVcselPulsePeriod(VL53L0X::VcselPeriodFinalRange, 14);
    tankSensor.setMeasurementTimingBudget(200000);
    Serial << "Distance sensor measuring" << endl;
    for (int readCnt = 0; readCnt < WATERSENSOR_CYCLE; readCnt++)
    
    {
      if (!tankSensor.timeoutOccurred())
      {
        uint16_t distance = tankSensor.readRangeSingleMillimeters();
        if (distance < MAX_TANK_DEPTH)
        {
          waterRawSensor.add(distance);
        }
      }
      delay(50);
    }
    Serial << "Distance sensor " << waterRawSensor.getMedian() << " mm" << endl;
  }
  else
  {
    log(LOG_LEVEL_WARN, LOG_TANKSENSOR_FAIL_DETECT, LOG_TANKSENSOR_FAIL_DETECT_CODE);
  }

  /* deactivate the sensors */
  digitalWrite(OUTPUT_ENABLE_SENSOR, LOW);
}

void onHomieEvent(const HomieEvent &event)
{
  switch (event.type)
  {
  case HomieEventType::READY_TO_SLEEP:
    esp_deep_sleep_start();
    break;
  case HomieEventType::SENDING_STATISTICS:
    break;
  case HomieEventType::MQTT_READY:
    if (mSensorsRead)
    {
      Serial.printf("Timeout occured... too late!\r\n");
      return;
    }
    mSensorsRead = true; // MQTT is working, deactivate timeout logic

    configTime(UTC_OFFSET_DE, UTF_OFFSET_DE_DST, ntpServer.get());
    startMQTTRoundtripTest();
    break;
  case HomieEventType::OTA_STARTED:
    for (int i = 0; i < MAX_PLANTS; i++)
    {
      mPlants[i].deactivatePump();
    }
    otaRunning = true;
    mDownloadMode = true;
    break;
  case HomieEventType::OTA_SUCCESSFUL:
    digitalWrite(OUTPUT_ENABLE_SENSOR, LOW);
    digitalWrite(OUTPUT_ENABLE_PUMP, LOW);
    ESP.restart();
    break;
  default:
    break;
  }
}
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
void loop()
{
  Homie.loop();
  /* Toggel Senor LED to visualize mode 3 */
  if (mDownloadMode)
  {
    if (nextBlink < millis())
    {
      digitalWrite(OUTPUT_ENABLE_SENSOR, !digitalRead(OUTPUT_ENABLE_SENSOR));
      if (mConfigured)
      {
        if (otaRunning)
        {
          nextBlink = millis() + 100;
        }
        else
        {
          nextBlink = millis() + 501;
        }
      }
      else
      {
        selfTest();
      }
    }
  }
  else
  {
    unsigned long timeSinceSetup = millis() - setupFinishedTimestamp;
    if ((timeSinceSetup > MQTT_TIMEOUT) && (!mSensorsRead))
    {
      mSensorsRead = true;
      /* Disable Wifi and put modem into sleep mode */
      WiFi.mode(WIFI_OFF);
      Serial << "Wifi mode set to " << WIFI_OFF << " mqqt was no reached within " << timeSinceSetup << "ms , fallback to offline mode " << endl;
      Serial.flush();
      plantcontrol();
    }
  }

  /** Timeout always stopping the ESP -> no endless power consumption */
  if (millis() > ESP_STALE_TIMEOUT && !mDownloadMode)
  {
    Serial << (millis() / 1000) << "not terminated watchdog reset" << endl;
    Serial.flush();
    esp_restart();
  }

  if (pumpToRun != -1)
  {
    pumpActiveLoop();
  }
}

/***
 * @fn plantcontrol
 * Main function, doing the logic
 */
void plantcontrol()
{
  if (aliveWasRead())
  {
    for (int i = 0; i < MAX_PLANTS; i++)
    {
      mPlants[i].postMQTTconnection();
      mPlants[i].setProperty("consecutivePumps").send(String(consecutiveWateringPlant[i]));
    }
  }

  readOneWireSensors();

  Serial << "W : " << waterRawSensor.getAverage() << " mm (" << String(waterLevelMax.get() - waterRawSensor.getAverage()) << " mm left)" << endl;

  mBatteryVoltage = battery.getVoltage(BATTSENSOR_INDEX_BATTERY);
  float chipTemp = battery.getTemperature();
  Serial << "Chip Temperatur " << chipTemp << " °C " << endl;

  if (aliveWasRead())
  {
    /* Publish water values, if available */
    if (waterRawSensor.getCount() > 0)
    {
      float remaining = (waterLevelMax.get() - waterRawSensor.getAverage());
      float actualDifference = waterLevelMax.get() - waterLevelMin.get();
      float ratio = remaining/actualDifference;
      sensorWater.setProperty("useable").send(String(actualDifference));
      if (!isnan(remaining))
      {
        /* measuring the distance from top -> smaller value means more water: */
        sensorWater.setProperty("remaining").send(String(ratio*100));
        
      }
      if (!isnan(waterRawSensor.getAverage()))
      {
        sensorWater.setProperty("distance").send(String(waterRawSensor.getAverage()));
      }
    }
    sensorLipo.setProperty("percent").send(String(100 * mBatteryVoltage / VOLT_MAX_BATT));
    sensorLipo.setProperty("volt").send(String(mBatteryVoltage));
    sensorLipo.setProperty("current").send(String(battery.getCurrent()));
    sensorLipo.setProperty("Ah").send(String(battery.getAh()));
    sensorLipo.setProperty("ICA").send(String(battery.getICA()));
    sensorLipo.setProperty("DCA").send(String(battery.getDCA()));
    sensorLipo.setProperty("CCA").send(String(battery.getCCA()));
    if (mSolarVoltage < SOLAR_MAX_VOLTAGE_POSSIBLE) {
      sensorSolar.setProperty("volt").send(String(mSolarVoltage));
    } else {
      log(LOG_LEVEL_INFO, String("Ignore unrealistc sun voltage" + String(mSolarVoltage) +"V"), LOG_SOLAR_CHARGER_MISSING);
    }
    sensorTemp.setProperty(TEMPERATUR_SENSOR_CHIP).send(String(chipTemp));
  }
  else
  {
    Serial.println("Skipping MQTT, offline mode");
    Serial.flush();
  }

bool isLowLight = (mSolarVoltage <= SOLAR_CHARGE_MAX_VOLTAGE);
#if defined(TIMED_LIGHT_PIN)
  
  bool shouldLight = determineTimedLightState(isLowLight);
  if(shouldLight){
    ulp_pwm_set_level(timedLightPowerLevel.get());
  }else {
    ulp_pwm_set_level(0);
  }

#endif // TIMED_LIGHT_PIN

  bool isLiquid = waterTemp > 5;
  bool hasWater = true; // By default activate the pump
  if (waterRawSensor.getCount() > 0)
  {
    //surface of water is still nearer the sensor than required to cover the pumps
    hasWater = waterRawSensor.getAverage() < waterLevelMin.get();
    if (waterRawSensor.getAverage() > waterLevelMax.get()) {
      log(LOG_LEVEL_ERROR, LOG_PUMP_FULLTANK_MESSAGE, LOG_PUMP_FULLTANK_CODE);
      hasWater = true;
    }
  }

  // FIXME no water warning message
  pumpToRun = determineNextPump(isLowLight);
  // early aborts
  if (pumpToRun != -1)
  {
    if(isLiquid){
      if (hasWater)
      {
        if (mDownloadMode)
        {
          log(LOG_LEVEL_INFO, LOG_PUMP_AND_DOWNLOADMODE, LOG_PUMP_AND_DOWNLOADMODE_CODE);
          pumpToRun = -1;
        } else {
          /* Pump can be used :) */
        }
      }
      else
      {
        log(LOG_LEVEL_ERROR, LOG_PUMP_BUTNOTANK_MESSAGE, LOG_PUMP_BUTNOTANK_CODE);
        pumpToRun = -1;
      }
    }
    else 
    {
        log(LOG_LEVEL_ERROR, LOG_VERY_COLD_WATER, LOG_VERY_COLD_WATER_CODE);
        pumpToRun = -1;
    }
  }

  // go directly to sleep, skipping the pump loop
  if (pumpToRun == -1)
  {
    espDeepSleep();
  }
}

/** @}*/

#ifdef TIMED_LIGHT_PIN
bool determineTimedLightState(bool lowLight)
{
  bool onlyAllowedWhenDark = timedLightOnlyWhenDark.get();
  long hoursStart = timedLightStart.get();
  long hoursEnd = timedLightEnd.get();

  // ntp missing
  if (getCurrentTime() < 10000)
  {
    timedLightNode.setProperty("state").send(String("Off, missing ntp"));
    return false;
  }
  if (onlyAllowedWhenDark && !lowLight)
  {
    timedLightNode.setProperty("state").send(String("Off, not dark"));
    timedLightLowVoltageTriggered = false;
    return false;
  }

  int curHour = getCurrentHour();

  bool condition1 = ((hoursStart > hoursEnd) &&
                     (curHour >= hoursStart || curHour <= hoursEnd));
  bool condition2 = /* Handle e.g. start = 8, end = 21 */

      ((hoursStart < hoursEnd) &&
       (curHour >= hoursStart && curHour <= hoursEnd));
  timedLightNode.setProperty("debug").send(String(curHour) + " " + String(hoursStart) + " " + String(hoursEnd) + " " + String(condition1) + " " + String(condition2));
  if (condition1 || condition2)
  {
    bool voltageOk = !timedLightLowVoltageTriggered && battery.getVoltage(BATTSENSOR_INDEX_BATTERY) >= timedLightVoltageCutoff.get();
    if (voltageOk || equalish(timedLightVoltageCutoff.get(), -1))
    {
      timedLightNode.setProperty("state").send(String("On"));
      return true;
    }
    else
    {
      timedLightNode.setProperty("state").send(String("Off, due to missing voltage"));
      timedLightLowVoltageTriggered = true;
      return false;
    }
  }
  else
  {
    timedLightNode.setProperty("state").send(String("Off, outside worktime"));
    return false;
  }
}

#endif

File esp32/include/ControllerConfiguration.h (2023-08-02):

/**
 * @file ControllerConfiguration.h
 * @author your name (you@domain.com)
 * @brief 
 * @version 0.1
 * @date 2020-05-30
 * 
 * @copyright Copyright (c) 2020
 * 
 * \mainpage Configuration of the controller
 * @{
 * Describe the used PINs of the controller
 *  
 * @subpage Controller
 * 
 * @subpage Homie
 * 
 * @subpage Configuration
 * 
 * There are several modes in the controller
 * \dot
 *  digraph Operationmode {
 *      ranksep=.75;
 *      poweroff [ label="off" ];
 *      mode1 [ label="Mode 1 - Sensor only", shape=box, width=2 ];
 *      mode2 [ label="Mode 2 - Wifi enabled", shape=box ];
 *      mode3 [ label="Mode 3 - Stay alive", shape=box ];
 *      mode1 -> mode2 [ label="wakeup reason", fontsize=10 ];
 *      mode1 -> mode2 [ label="Time duration", fontsize=10 ];
 *      mode2 -> mode3 [ label="Over the Air Update", fontsize=10 ];
 *      mode3 -> mode2 [ label="Over the Air Finished", fontsize=10 ];
 *      mode3 -> mode2 [ label="Mqtt Command", fontsize=10 ];
 *      mode2 -> mode3 [ label="Mqtt Command", fontsize=10 ];
 *      poweroff -> mode1 [ label="deep sleep wakeup", fontsize=10 ];
 *      mode1 -> poweroff [ label="enter deep sleep", fontsize=10 ];
 *      mode2 -> poweroff [ label="Mqtt queue empty", fontsize=10 ];
 *  }
 *  \enddot
 * 
 * Before entering Deep sleep the controller is configured with an wakeup time.
 * 
 * @}
 */
#ifndef CONTROLLER_CONFIG_H
#define CONTROLLER_CONFIG_H
/** \addtogroup GPIO Settings
 *  @{
 */
#define SENSOR_PLANT0 GPIO_NUM_32 /**< GPIO 32 (ADC1) */
#define SENSOR_PLANT1 GPIO_NUM_33 /**< GPIO 33 (ADC1) */
#define SENSOR_PLANT2 GPIO_NUM_25 /**< GPIO 25 (ADC2) */
#define SENSOR_PLANT3 GPIO_NUM_26 /**< GPIO 26 (ADC2) */
#define SENSOR_PLANT4 GPIO_NUM_27 /**< GPIO 27 (ADC2) */
#define SENSOR_PLANT5 GPIO_NUM_39 /**< SENSOR_VIN */
#define SENSOR_PLANT6 GPIO_NUM_36 /**< SENSOR_VP  */

#define OUTPUT_PUMP0 GPIO_NUM_15 /**< GPIO 15 */
#define OUTPUT_PUMP1 GPIO_NUM_5  /**< GPIO 5 */
#define OUTPUT_PUMP2 GPIO_NUM_18 /**< GPIO 18 */
#define OUTPUT_PUMP3 GPIO_NUM_19 /**< GPIO 19 */
#define OUTPUT_PUMP4 GPIO_NUM_21 /**< GPIO 21 */
#define OUTPUT_PUMP5 GPIO_NUM_22 /**< GPIO 22  */
#define OUTPUT_PUMP6 GPIO_NUM_23 /**< GPIO 23 */

#define OUTPUT_ENABLE_SENSOR GPIO_NUM_14 /**< GPIO 14 - Enable Sensors  */
#define OUTPUT_ENABLE_PUMP   GPIO_NUM_13 /**< GPIO 13 - Enable Pumps  */

#define SENSOR_ONEWIRE      GPIO_NUM_4 /**< GPIO 12 - Temperatur sensor, Battery and other cool onewire stuff */
#define SENSOR_TANK_SDA     GPIO_NUM_17 /**< GPIO 17 - water sensor SDA */ 
#define SENSOR_TANK_SCL     GPIO_NUM_16 /**< GPIO 16 - water sensor SCL */
#define BUTTON              GPIO_NUM_0  /**< GPIO 0 - Fix button of NodeMCU */

#define CUSTOM1_PIN1        GPIO_NUM_34   /** direct gpio */
#define CUSTOM1_PIN3        GPIO_NUM_35   /** direct gpio */
#define CUSTOM1_PIN5        GPIO_NUM_2   /** mosfet controlled */
#define CUSTOM1_PIN7        GPIO_NUM_12   /** mosfet controlled */

/* @} */

/** \addtogroup Configuration
 *  @{
 */

#ifdef FLOWMETER_PIN
    #define FLOWMETER_PULSES_PER_ML 2.2
    #define FIRMWARE_FEATURE1   "Flow"
#else
    #define FIRMWARE_FEATURE1   ""
#endif

#ifdef TIMED_LIGHT_PIN
    #define FIRMWARE_FEATURE2   "Light"
#else
    #define FIRMWARE_FEATURE2   ""
#endif

#define FIRMWARE_BASENAME "PlantControl"
#define FIRMWARE_NAME FIRMWARE_BASENAME FIRMWARE_FEATURE1 FIRMWARE_FEATURE2
#define FIRMWARE_VERSION "3.01 HW0.10b" 

#define MOIST_SENSOR_MAX_FRQ               5200 // 60kHz (500Hz margin)
#define MOIST_SENSOR_MIN_FRQ                500 // 0.5kHz (500Hz margin)

#define ANALOG_SENSOR_MAX_MV                1300 //successive approximation of good range
#define ANALOG_SENSOR_MIN_MV                100  //successive approximation of good range

#define SOLAR_VOLT_FACTOR           11
#define BATTSENSOR_INDEX_SOLAR      0
#define BATTSENSOR_INDEX_BATTERY    1

#define MQTT_TIMEOUT                (1000 * 60) /**< After 10 seconds, MQTT is expected to be connected */
#define ESP_STALE_TIMEOUT           (MQTT_TIMEOUT+(700*1000))

#define MAX_PLANTS          7
#define SOLAR_CHARGE_MIN_VOLTAGE    7   /**< Sun is rising (morning detected) */
#define SOLAR_CHARGE_MAX_VOLTAGE    9   /**< Sun is shining (noon)  */
#define SOLAR_MAX_VOLTAGE_POSSIBLE  100 /**< higher values are treated as not connected sensor  */
#define VOLT_MAX_BATT               4.2f
#define VOLT_MIN_BATT               3.0f    /**< Minimum battery voltage for normal operation */
#define LOWVOLT_SLEEP_FACTOR        3       /**< Factor for nightsleep delay, if the battery drops below minimum (@see VOLT_MIN_BATT) */
#define LOWVOLT_SLEEP_MINIMUM       1800    /**< At low voltage sleep at least for 30 minutes */

#define MAX_CONFIG_SETTING_ITEMS 100 /**< Parameter, that can be configured in Homie */
#define MAX_JSON_CONFIG_FILE_SIZE_CUSTOM 2500
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

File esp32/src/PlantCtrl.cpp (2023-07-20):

/**
 * @file PlantCtrl.cpp
 * @author your name (you@domain.com)
 * @brief
 * @version 0.1
 * @date 2020-05-27
 *
 * @copyright Copyright (c) 2020
 *

 */
#include "PlantCtrl.h"
#include "ControllerConfiguration.h"
#include "TimeUtils.h"
#include "driver/pcnt.h"
#include "MQTTUtils.h"

Plant::Plant(int pinSensor, int pinPump, int plantId, HomieNode *plant, PlantSettings_t *setting, SENSOR_MODE mode)
{
    this->mPinSensor = pinSensor;
    this->mPinPump = pinPump;
    this->mPlant = plant;
    this->mSetting = setting;
    this->mPlantId = plantId;
    this->mSensorMode = mode;
}

void Plant::init(void)
{
    /* Initialize Home Settings validator */
    this->mSetting->pSensorDry->setDefaultValue(DEACTIVATED_PLANT);
    this->mSetting->pSensorDry->setValidator([](long candidate)
                                             { return (((candidate >= 0.0) && (candidate <= 100.0)) || equalish(candidate, DEACTIVATED_PLANT) || equalish(candidate, HYDROPONIC_MODE) || equalish(candidate, TIMER_ONLY)); });

    this->mSetting->pPumpAllowedHourRangeStart->setDefaultValue(5); // start at 5:00 UTC or 7:00 ECST
    this->mSetting->pPumpAllowedHourRangeStart->setValidator([](long candidate)
                                                             { return ((candidate >= 0) && (candidate <= 23)); });
    this->mSetting->pPumpAllowedHourRangeEnd->setDefaultValue(18); // stop pumps at 18 UTC or 20:00 ECST
    this->mSetting->pPumpAllowedHourRangeEnd->setValidator([](long candidate)
                                                           { return ((candidate >= 0) && (candidate <= 23)); });
    this->mSetting->pPumpOnlyWhenLowLight->setDefaultValue(false);
    this->mSetting->pPumpCooldownInSeconds->setDefaultValue(60 * 60); // 1 hour
    this->mSetting->pPumpCooldownInSeconds->setValidator([](long candidate)
                                                         { return (candidate >= 0); });

    this->mSetting->pPumpDuration->setDefaultValue(30);
    this->mSetting->pPumpDuration->setValidator([](long candidate)
                                                { return ((candidate >= 0) && (candidate <= 1000)); });
    this->mSetting->pPumpMl->setDefaultValue(1000);
    this->mSetting->pPumpMl->setValidator([](long candidate)
                                          { return ((candidate >= 0) && (candidate <= 5000)); });
    this->mSetting->pPumpPowerLevel->setDefaultValue(100);
    this->mSetting->pPumpPowerLevel->setValidator([](long candidate)
                                                  { return ((candidate >= 0) && (candidate <= 100)); });

    /* Initialize Hardware */
    ledcSetup(this->mPlantId, PWM_FREQ, PWM_BITS);
    ledcAttachPin(mPinPump, this->mPlantId);
    ledcWrite(this->mPlantId, 0);
    pinMode(this->mPinSensor, INPUT);
}

void Plant::initSensors(void)
{
    switch (getSensorMode())
    {
    case FREQUENCY_MOD_RESISTANCE_PROBE:
    {

        pcnt_unit_t unit = (pcnt_unit_t)(PCNT_UNIT_0 + this->mPlantId);
        pcnt_config_t pcnt_config = {}; // Instancia PCNT config

        pcnt_config.pulse_gpio_num = this->mPinSensor; // Configura GPIO para entrada dos pulsos
        pcnt_config.ctrl_gpio_num = PCNT_PIN_NOT_USED; // Configura GPIO para controle da contagem
        pcnt_config.unit = unit;                       // Unidade de contagem PCNT - 0
        pcnt_config.channel = PCNT_CHANNEL_0;          // Canal de contagem PCNT - 0
        pcnt_config.counter_h_lim = INT16_MAX;         // Limite maximo de contagem - 20000
        pcnt_config.pos_mode = PCNT_COUNT_INC;         // Incrementa contagem na subida do pulso
        pcnt_config.neg_mode = PCNT_COUNT_DIS;         // Incrementa contagem na descida do pulso
        pcnt_config.lctrl_mode = PCNT_MODE_KEEP;       // PCNT - modo lctrl desabilitado
        pcnt_config.hctrl_mode = PCNT_MODE_KEEP;       // PCNT - modo hctrl - se HIGH conta incrementando
        pcnt_unit_config(&pcnt_config);                // Configura o contador PCNT

        pcnt_counter_pause(unit); // Pausa o contador PCNT
        pcnt_counter_clear(unit); // Zera o contador PCNT
        break;
    }
    case ANALOG_RESISTANCE_PROBE:
    {
        adcAttachPin(this->mPinSensor);
        break;
    }
    case NONE:
    {
        // do nothing
        break;
    }
    }
}

void Plant::blockingMoistureMeasurement(void)
{
    switch (getSensorMode())
    {
    case ANALOG_RESISTANCE_PROBE:
    {
        for (int i = 0; i < ANALOG_REREADS; i++)
        {
            this->mMoisture_raw.add(analogReadMilliVolts(this->mPinSensor));
            delay(5);
        }
        break;
    }
    case FREQUENCY_MOD_RESISTANCE_PROBE:
    case NONE:
    {
        // nothing to do here
        break;
    }
    }
}

void Plant::startMoistureMeasurement(void)
{
    switch (getSensorMode())
    {
    case FREQUENCY_MOD_RESISTANCE_PROBE:
    {
        pcnt_unit_t unit = (pcnt_unit_t)(PCNT_UNIT_0 + this->mPlantId);
        pcnt_counter_resume(unit);
        break;
    }
    case ANALOG_RESISTANCE_PROBE:
    case NONE:
    {
        // do nothing here
    }
    }
}

void Plant::stopMoistureMeasurement(void)
{
    switch (getSensorMode())
    {
    case FREQUENCY_MOD_RESISTANCE_PROBE:
    {
        int16_t pulses;
        pcnt_unit_t unit = (pcnt_unit_t)(PCNT_UNIT_0 + this->mPlantId);
        pcnt_counter_pause(unit);
        esp_err_t result = pcnt_get_counter_value(unit, &pulses);
        pcnt_counter_clear(unit);
        if (result != ESP_OK)
        {
            log(LOG_LEVEL_ERROR, LOG_HARDWARECOUNTER_ERROR_MESSAGE, LOG_HARDWARECOUNTER_ERROR_CODE);
            this->mMoisture_raw.clear();
            this->mMoisture_raw.add(-1);
        }
        else
        {
            this->mMoisture_raw.add(pulses * (1000 / MOISTURE_MEASUREMENT_DURATION));
        }
        break;
    }
    case ANALOG_RESISTANCE_PROBE:
    case NONE:
    {
        break;
    }
    }
}
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

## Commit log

2020-09-07 changed footprint to actual one
    [PlantCtrlESP32.kicad_pcb, PlantCtrlESP32.sch]
2020-09-07 Removed resistor
    [PlantCtrlESP32.sch]
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2020-09-12 updated shematic for new version
    [PlantCtrlESP32.sch]
2020-09-14 Schematic Draft finished; Routing started
    [PlantCtrlESP32.kicad_pcb, PlantCtrlESP32.sch]
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2020-09-19 It is Pump, not Pump1 for the LED; Same for Sensors
    [PlantCtrlESP32.kicad_pcb, PlantCtrlESP32.sch]
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2020-10-14 fixed pcb layout
    [PlantCtrlESP32-drl_map.dxf, PlantCtrlESP32.kicad_pcb, PlantCtrlESP32.sch]
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2020-10-16 Modes still not working
    [main.cpp]
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2020-10-20 partitions with slightly more flash and smaller spiffs
    [defaultWithSmallerSpiffs.csv]
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2020-10-23 * Es gibt lange Leitungen die von der Platine weg gehen. Hier gibt es zwei Risiken: - Sie können sich Hochfrequente Störungen aus der Umgebung einfangen (sie bilden letztlich eine große Antenne) --> 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
    [PlantCtrlESP32.sch]
2020-10-23 Only Pump safety is not placed
    [PlantCtrlESP32.kicad_pcb, PlantCtrlESP32.sch]
2020-10-28 Power for Pump is disabled if no longer required
    [ControllerConfiguration.h, main.cpp]
2020-10-28 Pump5 pin corrected
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2020-10-29 Moved more parts arround
    [PlantCtrlESP32.kicad_pcb]
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2020-10-30 OneWire pin and Temp sensor use both sensorpower
    [PlantCtrlESP32.sch]
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2020-10-31 SensorPwr for 1Wire routed
    [PlantCtrlESP32.kicad_pcb]
2020-10-31 made deep sleep modes work and behave somewhat correctly, gave mqqt time to publish, gave ntp time to sync
    [main.cpp]
2020-11-01 Fixed plant loop in mode1
    [main.cpp]
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2020-11-04 fixed wrong indes for pump determination improved pump status output fixed led blinking in mode3 random
    [PlantCtrl.h, main.cpp]
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2020-11-04 missing sensor detection, delta trigger moisture working
    [ControllerConfiguration.h, HomieConfiguration.h, HomieTypes.h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]
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2020-11-07 moved solar connector more to border
    [PlantCtrlESP32.kicad_pcb]
2020-11-11 Added Lipo protection into schematic
    [PlantCtrlESP32.sch]
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2020-11-11 added lipo protector to schematic
    [PlantCtrlESP32.kicad_pcb, PlantCtrlESP32.sch]
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2020-11-18 replaced HC-SR04 with SR04M-2
    [ControllerConfiguration.h, main.cpp]
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2020-11-27 routing and schematic fixes
    [PlantCtrlESP32.kicad_pcb, PlantCtrlESP32.sch]
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2020-12-02 fixed wrong mosefets used
    [PlantCtrlESP32.kicad_pcb, PlantCtrlESP32.sch]
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2020-12-09 Fixed wakeup due static code analysis
    [main.cpp]
2020-12-09 All static code analyis comments fixed, only TODOs are open
    [main.cpp]
2020-12-11 prevent infinite loop on waiting for hall if not connected, fixed formating
    [main.cpp]
2020-12-12 fixed pin assignements for new revision
    [ControllerConfiguration.h]
2020-12-13 fix one wire detection, allow multiple sensors and set per setting which one is which
    [HomieConfiguration.h, main.cpp]
2020-12-20 Replaced N-Channel Mosfets part number with the expected one
    [PlantCtrlESP32.sch]
2020-12-20 Missed one N-Channel Mosfet
    [PlantCtrlESP32.sch]
2020-12-20 Fixed Mosfet used to switch Pump and Sensor supply
    [PlantCtrlESP32.sch]
2020-12-20 pin fix
2020-12-21 Added capacitor for ESP
    [PlantCtrlESP32.kicad_pcb, PlantCtrlESP32.sch]
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2020-12-21 Used distance reading time to stabilize temperature sensors
    [ControllerConfiguration.h, main.cpp]
2020-12-24 fix for upstepper inductor, fix upstepper diode, fix voltage on pumps when upstepper is off
    [PlantCtrlESP32.sch]
2020-12-28 Moved Pump Voltage Converter to other circuit
    [PlantCtrlESP32.sch]
2020-12-28 Moved J6 under lipo
    [PlantCtrlESP32.kicad_pcb]
2020-12-28 Removed deadend wires at S6
    [PlantCtrlESP32.kicad_pcb]
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2020-12-28 Fixed one-wire library with an hammer
    [ControllerConfiguration.h, main.cpp]
2020-12-30 Added J8 for USB programming and POWER supply by USB; Lipo has to be disconnected!
    [PlantCtrlESP32.kicad_pcb, PlantCtrlESP32.sch]
2021-01-05 Renamed Lipo+ to VCC
    [PlantCtrlESP32.sch]
2021-01-05 Solar charger and lipo protection seperated
    [PlantCtrlESP32.sch]
2021-01-05 Replaced ESP module with WROOM-32D chip
    [PlantCtrlESP32.sch]
2021-01-05 External 5V no longer exists
    [PlantCtrlESP32.sch]
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2021-01-05 Fuse holder replaced
    [PlantCtrlESP32.kicad_pcb, PlantCtrlESP32.sch]
2021-01-05 Added referencal voltages at SENSOR_VP and SENSOR_VN
    [PlantCtrlESP32.sch]
2021-01-05 swapped moister sensor pins
    [PlantCtrlESP32.sch]
2021-01-05 solder jumper at Hall1 changed to NC
    [PlantCtrlESP32.sch]
2021-01-05 Swapped IO15 with IO17
    [PlantCtrlESP32.sch]
2021-01-05 IC1 VDD is protected by the fuse F1, too
    [PlantCtrlESP32.sch]
2021-01-05 SENSOR_VP and SENSOR_VN has 100n capacitor
    [PlantCtrlESP32.sch]
2021-01-05 Described external power supply
    [PlantCtrlESP32.sch]
2021-01-05 Custom connection connector removed solder jumper and pullup resistor
    [PlantCtrlESP32.sch]
2021-01-12 integrated battery management chip
    [PlantCtrlESP32.sch]
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2021-01-13 added alternative lipo connector
    [PlantCtrlESP32.sch]
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2021-01-13 References updated: readable and position on PCB
    [PlantCtrlESP32.kicad_pcb, PlantCtrlESP32.sch]
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2021-01-13 fixed LCSC part numbers
    [PlantCtrlESP32.sch]
2021-01-30 BOM for Board 0.7
    [PlantCtrlESP32_Board0_7.ods]
2021-01-30 Last minute fixes while assembly
    [PlantCtrlESP32.kicad_pcb, PlantCtrlESP32.sch, PlantCtrlESP32_Board0_7.ods]
2021-01-30 Swapped GPIO2 with GPIO12
    [PlantCtrlESP32.sch]
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2021-02-04 ds2438 stuff, vesense+ and - swapped
    [PlantCtrlESP32.kicad_pcb, PlantCtrlESP32.sch]
2021-02-06 added pump converter stabilisation CP's value determined via scope
    [PlantCtrlESP32.sch]
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2021-02-09 hall via softserial, vsense wrong direction
    [PlantCtrlESP32.sch]
2021-02-09 automatic ESP32 download mode added
    [PlantCtrlESP32.sch]
2021-02-09 Changed Transistors from THT to SMD
    [PlantCtrlESP32.sch]
2021-02-09 J1 has now a footprint
    [PlantCtrlESP32.sch]
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2021-02-09 Debug point got footprint
    [PlantCtrlESP32.sch]
2021-02-09 updated pcb to chematic
    [PlantCtrlESP32.kicad_pcb]
2021-02-09 battery stabilizer capacitor, named switches
    [PlantCtrlESP32.kicad_pcb, PlantCtrlESP32.sch]
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2021-02-12 use correct footprints for oven soldering
    [PlantCtrlESP32.kicad_pcb, PlantCtrlESP32.sch]
2021-02-16 green led less annoying
    [PlantCtrlESP32.sch]
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2021-02-16 Corrected pin configuration to 0.7final PCB
    [ControllerConfiguration.h, main.cpp]
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2021-02-24 Reduced sensor led brightness
    [PlantCtrlESP32.sch]
2021-02-26 removed mode1, reduced redundant bus resets, removed multiple deep sleep paths
    [ControllerConfiguration.h, main.cpp]
2021-03-02 Added serial2 of ESP32 useable for JSN-SR04T-2.0
    [PlantCtrlESP32.sch]
2021-03-04 Shunt set to 25mOhm
    [PlantCtrlESP32.sch]
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2021-03-04 use serial2 for hall, simplified gpio2/custom pio header, simplified low discharge protection
    [PlantCtrlESP32.sch]
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2021-05-16 Fix labels in pcb
    [PlantCtrlESP32.kicad_pcb, PlantCtrlESP32.sch]
2021-05-16 Describe different buttons should be used
    [PlantCtrlESP32.sch]
2021-05-16 Nchannel is not Pchannel!
    [PlantCtrlESP32.sch]
2021-05-16 Todos after building revision
    [PlantCtrlESP32.sch]
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2021-05-24 control works again (fixed with wifi and fallback)
    [PlantCtrl.cpp, main.cpp]
2021-05-24 fixed deepsleep procedure, homie shutdown, ensure pinhold is same as pin
    [ControllerConfiguration.h, main.cpp]
2021-05-24 fixed homie config fail mode
    [main.cpp]
2021-05-26 more capacitors, slight layout optimisation
    [PlantCtrlESP32.kicad_pcb, PlantCtrlESP32.sch]
2021-05-26 added testmode, fixed formating
    [PlantCtrl.cpp, main.cpp]
2021-05-27 retry on crc error for onewire
    [DS2438.cpp, main.cpp]
2021-05-28 changed switches to cheaper alternative
    [PlantCtrlESP32.kicad_pcb, PlantCtrlESP32.sch]
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2021-05-29 ensure DS18S20 are properly resolved via address
    [main.cpp]
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2021-06-01 fixed power on download mode, solar voltage sensor fixed
    [PlantCtrlESP32.kicad_pcb, PlantCtrlESP32.sch]
2021-06-01 fixed labeling and spacing for sensors and pumps
    [PlantCtrlESP32.kicad_pcb]
2021-06-02 use same pinout for moisture sensor as used on the sensor itself
    [PlantCtrlESP32.kicad_pcb, PlantCtrlESP32.sch]
2021-06-04 add high impendance pulldown to analog in
    [PlantCtrlESP32.kicad_pcb, PlantCtrlESP32.sch]
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2021-06-04 further reduced only once used parts
    [PlantCtrlESP32.kicad_pcb, PlantCtrlESP32.sch]
2021-06-06 added more correct pull down for download mode
    [PlantCtrlESP32.kicad_pcb, PlantCtrlESP32.sch]
2021-06-06 fixed bootloader
    [PlantCtrlESP32.sch]
2021-06-06 added distance sensor and adjusted pcb for it
    [PlantCtrlESP32.kicad_pcb, PlantCtrlESP32.sch]
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2021-06-10 redesigned custom connector
    [PlantCtrlESP32.sch]
2021-06-10 new extension header, improved labeling of connectors, optimized layout
    [PlantCtrlESP32.kicad_pcb, PlantCtrlESP32.sch]
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2021-06-23 Set 2k2 as pullup for I2C
    [PlantCtrlESP32.kicad_pcb, PlantCtrlESP32.sch]
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2021-06-29 stop then script from sleeping the esp in case of an error
2021-06-29 fixed config backup and restore
    [FileUtils.cpp, main.cpp]
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2021-07-01 Fixed concatination of strings in logging
    [main.cpp]
2021-07-01 fix cooldown memory without power, improved logging
    [LogDefines.h, main.cpp]
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2021-07-21 missing sensor error
2021-08-17 fixed wrong percent calculation, emit trigger value to mqtt
    [PlantCtrl.cpp, PlantCtrl.h]
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2021-08-30 fix for wrong validator
    [main.cpp]
2021-09-14 prevent light from being reenabled untill next day after low voltage trigger
    [ControllerConfiguration.h, main.cpp]
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2021-10-26 some fixes for hydroponics mode
    [ControllerConfiguration.h, LogDefines.h, PlantCtrl.cpp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]
2021-10-26 use shorter valid firmeware name
    [ControllerConfiguration.h]
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2021-10-26 fix for hydroponic not working at night
    [PlantCtrl.h]
2021-10-26 properly set last run time, as it apparently was missing
    [main.cpp]
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2021-10-27 added epoxy form and sensor mod
    [verguss form sensor v1.stl]
2021-10-27 increased ota flash sizes
    [defaultWithSmallerSpiffs.csv]
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2022-02-19 fix for capacitive sensors not working, enum introduction for sensormode
    [ControllerConfiguration.h, HomieTypes.h, PlantCtrl.cpp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]
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2022-03-06 Swapped max and min for analog mapping
    [PlantCtrl.h]
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2022-04-29 fixed analog probe being backwards, extended range for frequency one
    [ControllerConfiguration.h, PlantCtrl.h]
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2022-08-22 Fixed unit description for cooldown
    [HomieConfiguration.h]
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2023-02-10 fix water error code
    [LogDefines.h, main.cpp]
2023-02-12 Revert "add resistive frequency sensor, updated dependencies"
    This reverts commit 17d16a6eef60715fb64cfeeff4c81baf43ddd5d1.
    [ControllerConfiguration.h, HomieTypes.h, PlantCtrl.cpp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]
2023-02-12 Revert "Revert "add resistive frequency sensor, updated dependencies""
    This reverts commit 42ce4cdda2ae521129661115d4b381f6dfabae46.
    [ControllerConfiguration.h, HomieTypes.h, PlantCtrl.cpp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]
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2023-03-22 Reset sensor on bad values
    [main.cpp]
2023-03-22 Reset as distance is > 8 meter
    [main.cpp]
2023-03-22 distance sensor is reset after powercycle
    [main.cpp]
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2023-03-22 Swapped water sensor pins
    [ControllerConfiguration.h]
2023-03-24 Fixed water distance and publish percentage
    [main.cpp]
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2023-04-26 fixed not watering when water is left
    [main.cpp]
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2023-05-27 More serial debuging (parsing 1WIRE Addresses failed)
    [main.cpp]
2023-06-04 Fix remaining mqtt calculation
    [main.cpp]
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2023-08-02 increase ota partition size for newer platform core
    [defaultWithSmallerSpiffs.csv]

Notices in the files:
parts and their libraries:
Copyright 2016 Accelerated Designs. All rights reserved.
